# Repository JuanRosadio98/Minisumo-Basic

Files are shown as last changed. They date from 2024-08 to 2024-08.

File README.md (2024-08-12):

# Minisumo Nivel Senior
Robot Minisumo basado en ESP32, driver TB6612FNG, sensores JS40F y Qtr1A para principiantes en robotica de competencia

DIAGRAMA DE BLOQUES DE COMPONENTES DEL ROBOT



VISTS 3D DE ROBOT ENSAMBLADO



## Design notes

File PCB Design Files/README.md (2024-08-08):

- Esquematico

  Ruta: ESP32_RobotController_Modular\Project Outputs\Documentation
- Bottom Layer para imprimir

  Ruta: ESP32_RobotController_Modular\Project Outputs\Documentation
- Lista de materiales (BOM)

  Ruta: ESP32_RobotController_Modular\Project Outputs\Assembly
- Archivos de fabricacion (Gerbers)

  Ruta: ESP32_RobotController_Modular\Project Outputs\Fabrication





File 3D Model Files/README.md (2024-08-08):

Materiales recomendados: ABS, PETG, PLA

Materiales adiconales para el ensamble:
. 6 Tornillos M3 x 10mm
  Referencia: 
  
  https://es.aliexpress.com/item/1005005483354397.html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

- 4 Prisioneros M3 x 4mm
  Referencia:
  
  https://es.aliexpress.com/item/1005006790023154.html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,scm-url:1007.40050.354490.0,pvid:8e516edc-514a-40b4-a4dc-20a4244071bc,tpp_buckets:668%232846%238109%231935&pdp_npi=4%40dis%21PEN%212.44%211.44%21%21%214.53%212.67%21%40210324e517231562863025298e5644%2112000038308083836%21rec%21PE%21%21ABX&utparam-url=scene%3ApcDetailTopMoreOtherSeller%7Cquery_from%3A

Piezas impresas en 3D ensambladas:



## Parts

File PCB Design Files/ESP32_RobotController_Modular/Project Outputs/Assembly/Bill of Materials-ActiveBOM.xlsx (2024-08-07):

Name | Description | Designator | Quantity
220uF, 50V | WCAP-ATG8 Aluminum Electrolytic Capacitor, Radial, THT, D10xH12.5, 220uF, 50V | C1 | 1
47uF, 50V | WCAP-ATG8 Aluminum Electrolytic Capacitor, Radial, THT, D6.3xH11, 47uF, 50V | C2 | 1
Diode Schottky | Diodo Schottky SS36 3A 60 V | D1 | 1
Header 3P | WR-PHD Socket Header, THT, Vertical, pitch 2.54mm, 1 Row, 3P | J1, J2, J3, J4, J5, J6, J7 | 7
Bornera de 2 pines | WR-TBL Serie 111 Horizontal Entry Modular, Pressure Clamp, THT, pitch 5mm, 2p | J8, J9, J10 | 3
Header 4p | WR-PHD Socket Header, THT, pitch 2.54mm, Single Row, Vertical, 4p | J12 | 1
Resistor 0805 | SMD 0805 10Kohms | R1, R2, R3, R4, R5, R6, R7, R15, R16, R17 | 10
Resistor 0805 | SMD 0805 20Kohms | R8, R9, R10, R11, R12, R13, R14 | 7
XUNPU TS-1002S-07026C | 6mm 7mm Round Button 50mA Brick nogging 6mm SPST 12V SMD,6x6mm Tactile Switches ROHS | SW1, SW2, SW3 | 3
7805 SMD TO-252 | IC REG LINEAR 5V 1A DPAK | U1 | 1
TB6612FNG - Module | Driver Puente H TB6612FNG 1.2A | U2 | 1
ESP32 DevkitV1 | ESP32 DEVKIT V1 Wireless WiFi Bluetooth Placa de desarrollo Micro USB Dual Core | U3 | 1

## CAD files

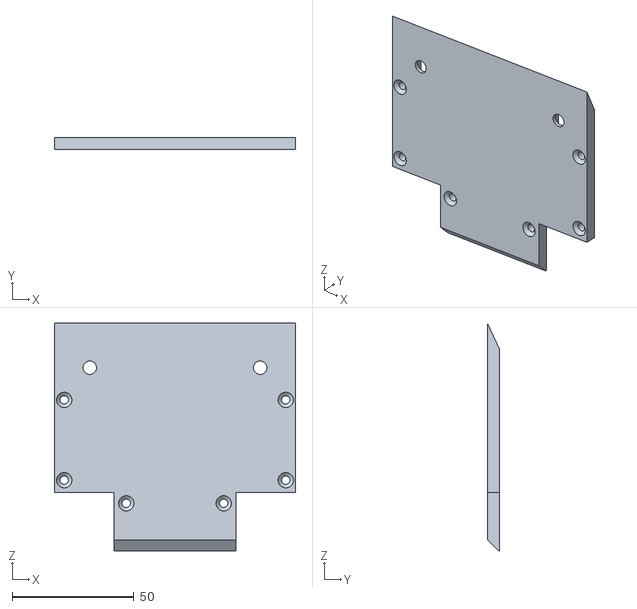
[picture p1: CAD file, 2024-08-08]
3D Model Files/STL/BaseTotal.stl
99.0 x 5.00 x 93.5

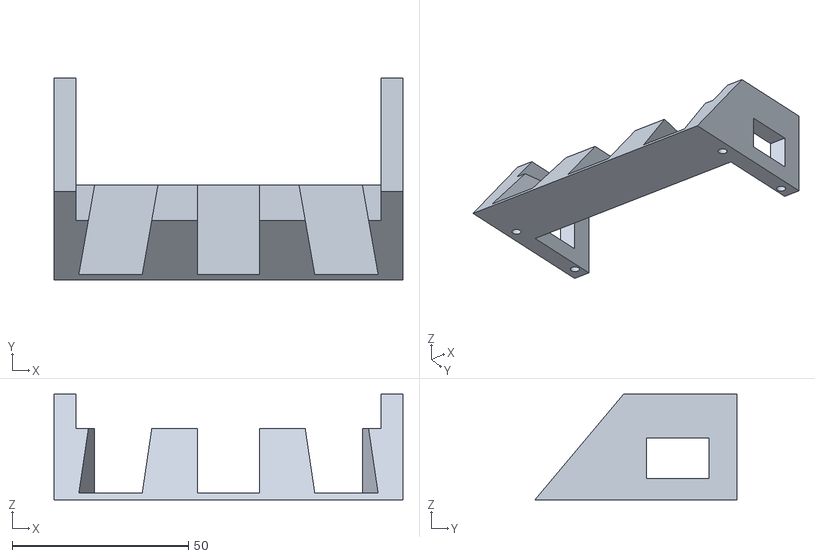
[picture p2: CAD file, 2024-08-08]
3D Model Files/STL/Cuerpo.stl
99.0 x 57.4 x 30.0

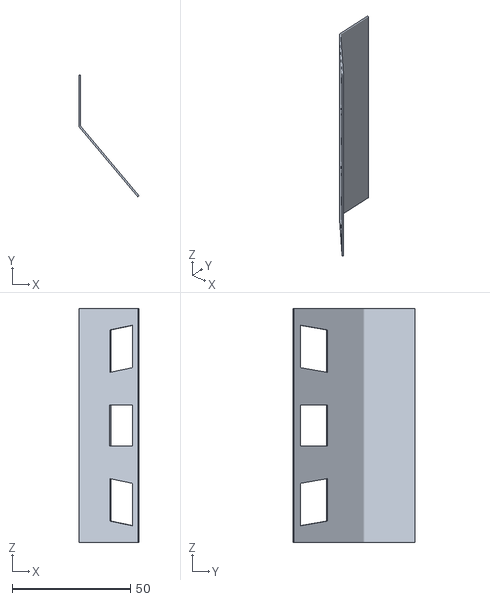
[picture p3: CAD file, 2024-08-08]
3D Model Files/STL/Cara.stl
25.4 x 51.5 x 99.0

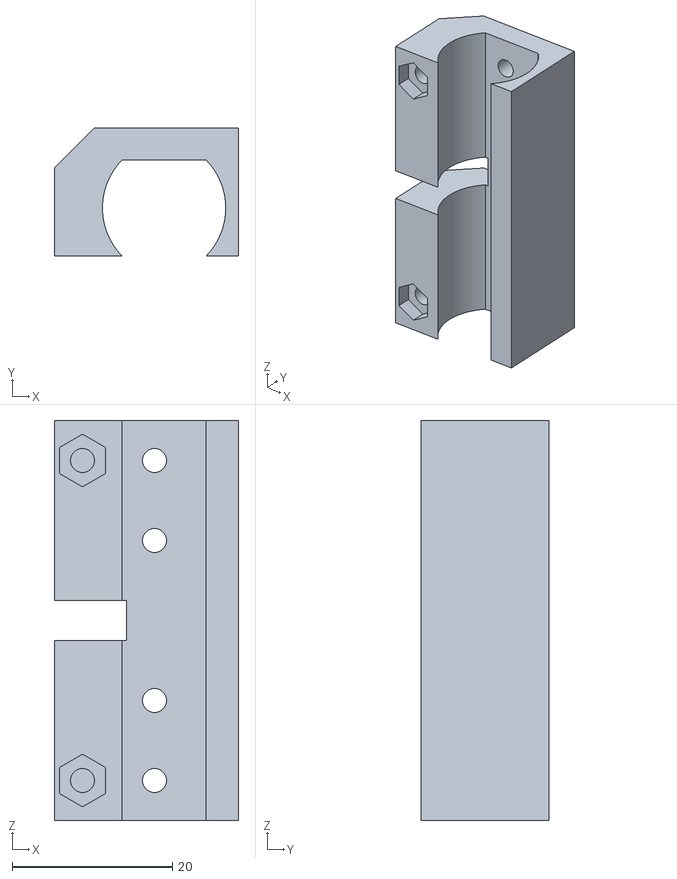
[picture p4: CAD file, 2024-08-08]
3D Model Files/STL/CajadeMotores Novamax H.stl
23.0 x 16.0 x 50.0

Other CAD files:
3D Model Files/BaseTotal.ipt
3D Model Files/CajadeMotores Novamax H.ipt
3D Model Files/Cara.ipt
3D Model Files/Cuerpo.ipt
3D Model Files/Ensamble.iam
3D Model Files/OldVersions/Ensamble.0001.iam

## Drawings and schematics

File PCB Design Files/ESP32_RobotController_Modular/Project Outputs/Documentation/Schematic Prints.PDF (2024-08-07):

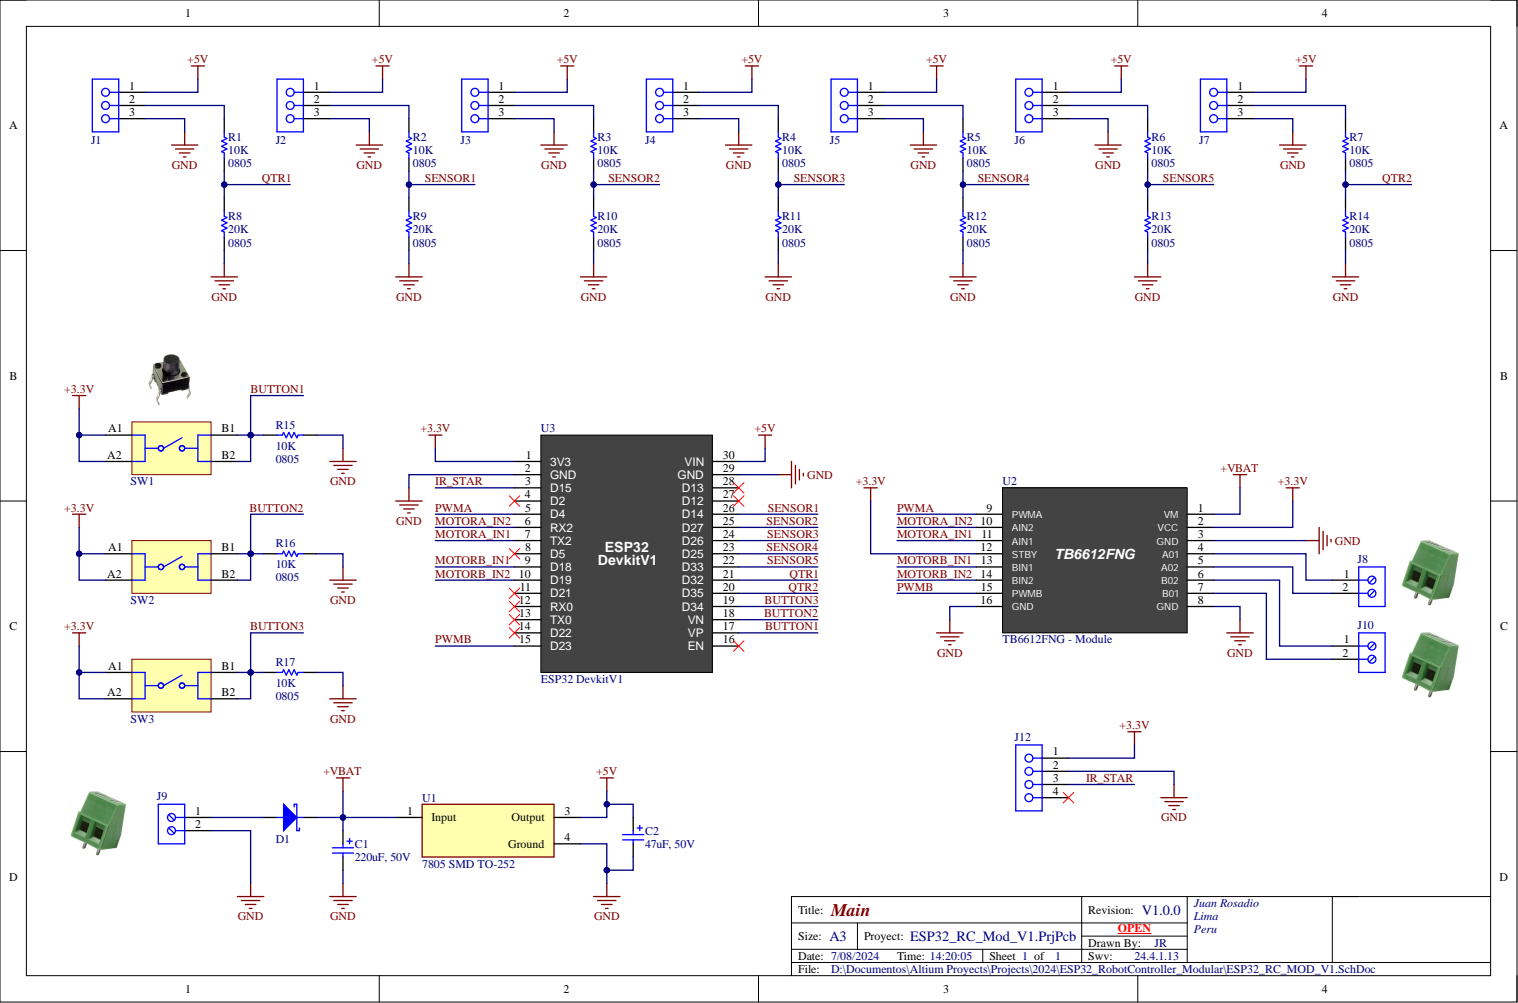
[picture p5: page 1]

D:\Documentos\Altium Proyects\Projects\2024\ESP32_RobotController_Modular\ESP32_RC_MOD_V1.SchDoc

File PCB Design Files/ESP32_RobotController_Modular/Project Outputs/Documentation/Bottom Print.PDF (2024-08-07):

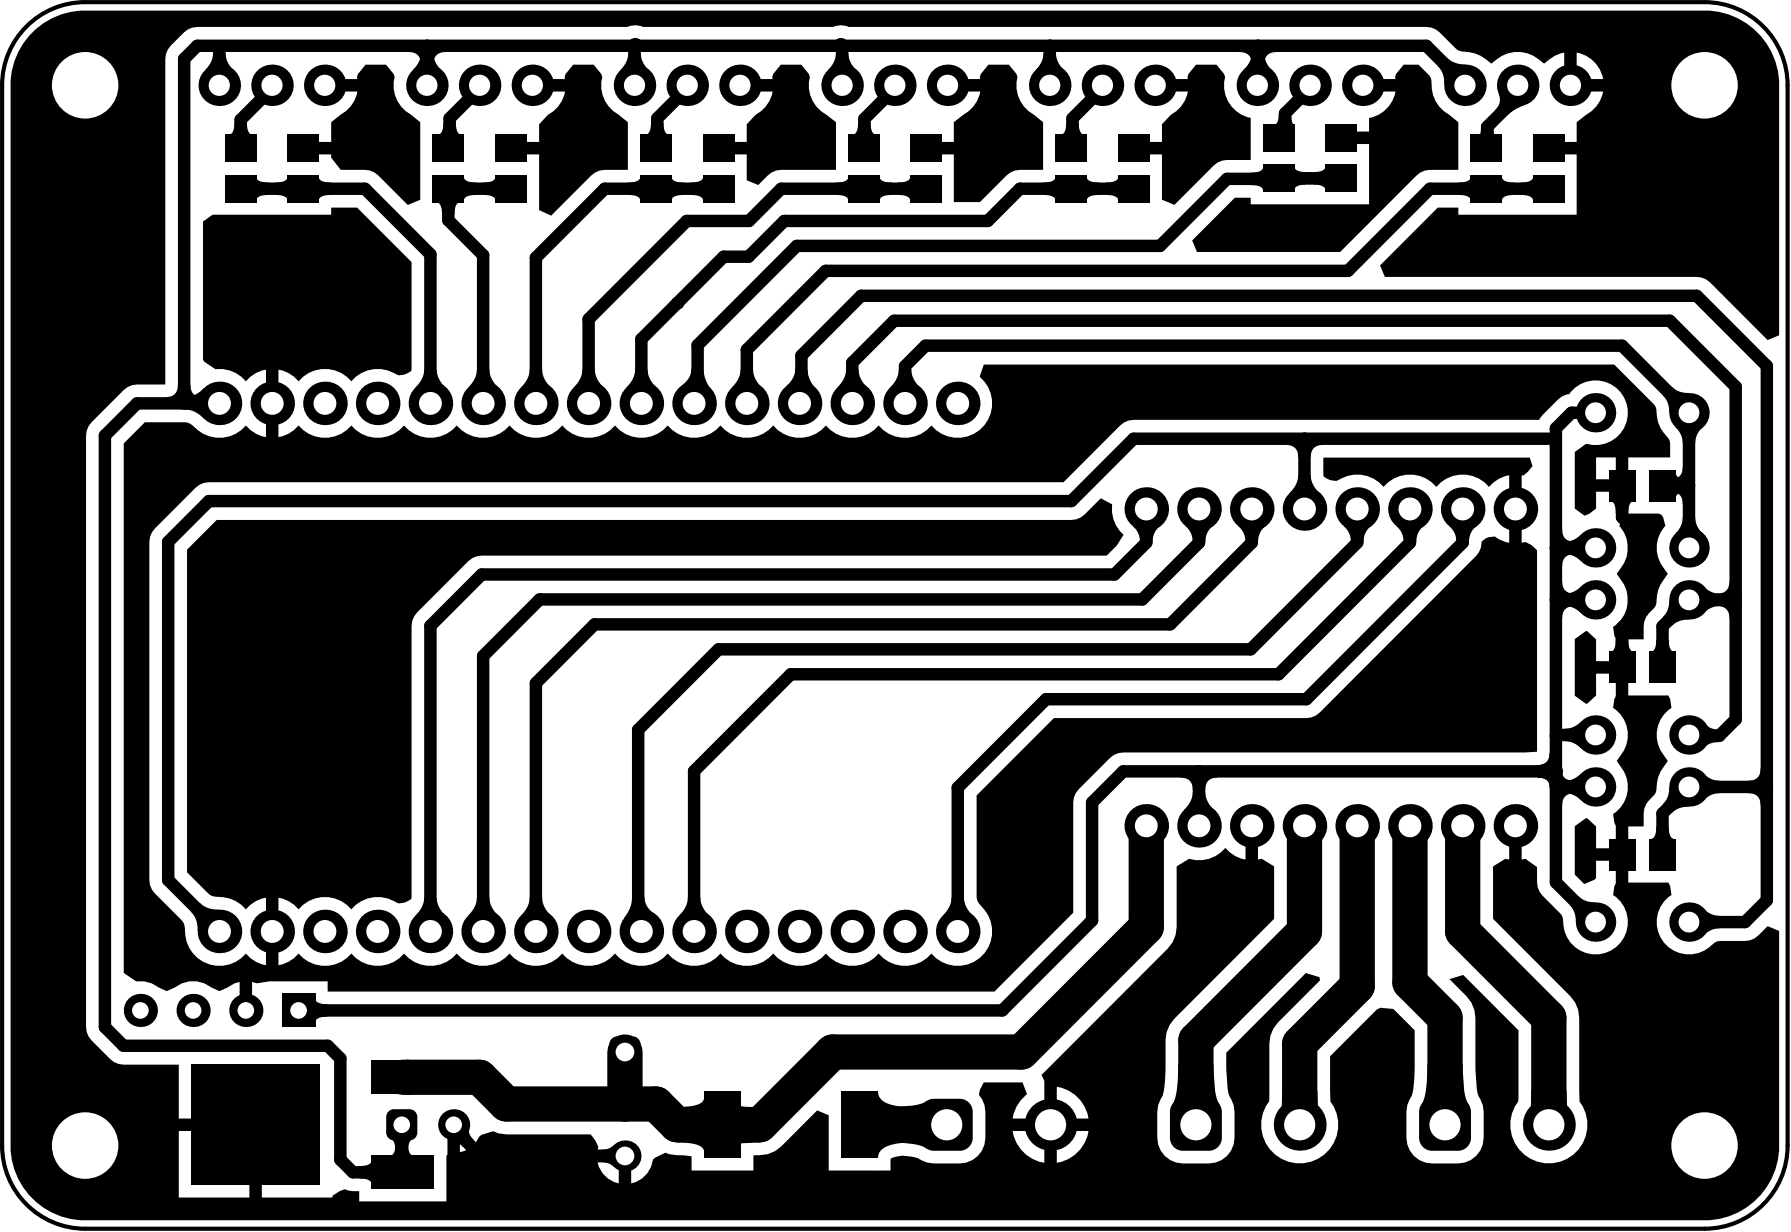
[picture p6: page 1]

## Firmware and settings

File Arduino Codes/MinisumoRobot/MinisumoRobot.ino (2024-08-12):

#define PUSH_1 36
#define PUSH_2 39
#define PUSH_3 34
//LINE SENSORS
#define QTR_1 32
#define QTR_2 35
//PRESENCE SENSORS
#define SENSOR_1 14
#define SENSOR_2 27
#define SENSOR_3 26
#define SENSOR_4 25
#define SENSOR_5 33

//REMOTE CONTROL
#define IR_STAR 15

#define USER_LED 2

//MOTOR DRIVER
#define MOTOR_PWMA 4
#define MOTOR_INA1 17
#define MOTOR_INA2 16

#define MOTOR_PWMB 23
#define MOTOR_INB1 18
#define MOTOR_INB2 19

#define TmCh_PWMA 0
#define TmCh_PWMB 1

int s_ii, s_i, s_c, s_d, s_dd, qtr_i, qtr_d, ctrl_star;
int strategy = 0;

void Push_Init(void);
void Motors_Init(void);
void Sensors_Init(void);

void setup() {
  // put your setup code here, to run once:
  Serial.begin(115200);
  Push_Init();
  Motors_Init();
  Sensors_Init();
  digitalWrite(USER_LED, LOW);

  Serial.println("Seleccione Estrategia(1-3): ");
  while (1) {
    if (digitalRead(PUSH_1) == 1) {
      digitalWrite(USER_LED, HIGH);
      while (1) {
        if (digitalRead(PUSH_1) == 0) {
          strategy++;
          digitalWrite(USER_LED, LOW);
          Serial.println(strategy);
          break;
        }
      }
    }

    if (digitalRead(PUSH_2) == 1 && strategy > 0) {
      digitalWrite(USER_LED, HIGH);
      while (1) {
        if (digitalRead(PUSH_2) == 0) {
          strategy--;
          digitalWrite(USER_LED, LOW);
          Serial.println(strategy);
          break;
        }
      }
    }

    if (digitalRead(PUSH_3) == 1) {
      while (1) {
        if (digitalRead(PUSH_3) == 0) {
          for (int i = 0; i < strategy; i++) {
            digitalWrite(USER_LED, HIGH);
            delay(500);
            digitalWrite(USER_LED, LOW);
            delay(400);
          }
          break;
        }
      }
      break;
    }
  }
  Serial.print("Strategy selected: ");
  Serial.println(strategy);

  while (ctrl_star == 0) {
    digitalWrite(USER_LED, HIGH);
    delay(100);
    digitalWrite(USER_LED, LOW);
    delay(100);
    Sensors_Read();
  }
}

void loop() {
  // put your main code here, to run repeatedly:
  switch (strategy) {
    case 1:
      Strategy_1();
      break;

    case 2:
      Strategy_2();
      break;

    case 3:
      Strategy_3();
      break;

    default:
      break;
  }
}

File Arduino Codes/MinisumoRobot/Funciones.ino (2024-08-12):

void Sensors_Read(void) {
  s_ii = digitalRead(SENSOR_1);
  s_i = digitalRead(SENSOR_2);
  s_c = digitalRead(SENSOR_3);
  s_d = digitalRead(SENSOR_4);
  s_dd = digitalRead(SENSOR_5);

  qtr_i = digitalRead(QTR_1);
  qtr_d = digitalRead(QTR_2);

  ctrl_star = digitalRead(IR_STAR);
}

void Sensors_Init(void) {
  pinMode(SENSOR_1, INPUT);
  pinMode(SENSOR_2, INPUT);
  pinMode(SENSOR_3, INPUT);
  pinMode(SENSOR_4, INPUT);
  pinMode(SENSOR_5, INPUT);

  pinMode(QTR_1, INPUT);
  pinMode(QTR_2, INPUT);

  pinMode(IR_STAR, INPUT);
}

void Push_Init(void){
  pinMode(PUSH_1, INPUT);
  pinMode(PUSH_2, INPUT);
  pinMode(PUSH_3, INPUT);
}

void Motors_Init(void)
{
  //Canal del Timer, Freq, Resolution
  ledcSetup(TmCh_PWMA, 10000, 10);
  ledcSetup(TmCh_PWMB, 10000, 10);
  //Pin, Canal del Timer
  ledcAttachPin(MOTOR_PWMA, TmCh_PWMA);
  ledcAttachPin(MOTOR_PWMB, TmCh_PWMB);

  pinMode(MOTOR_INA1, OUTPUT);
  pinMode(MOTOR_INA2, OUTPUT);
  pinMode(MOTOR_INB1, OUTPUT);
  pinMode(MOTOR_INB2, OUTPUT);

  digitalWrite(MOTOR_INA1, LOW);
  digitalWrite(MOTOR_INA2, LOW);
  digitalWrite(MOTOR_INB1, LOW);
  digitalWrite(MOTOR_INB2, LOW);

}

void Motors_Control(int pwmA, int pwmB)
{
  if (pwmA >= 0)
  {
    ledcWrite(TmCh_PWMA, pwmA);
    digitalWrite(MOTOR_INA1, LOW);
    digitalWrite(MOTOR_INA2, HIGH);
  }
  else
  {
    pwmA = pwmA * -1;
    ledcWrite(TmCh_PWMA, pwmA);
    digitalWrite(MOTOR_INA1, HIGH);
    digitalWrite(MOTOR_INA2, LOW);
  }

  if (pwmB >= 0)
  {
    ledcWrite(TmCh_PWMB, pwmB);
    digitalWrite(MOTOR_INB1, LOW);
    digitalWrite(MOTOR_INB2, HIGH);
  }
  else
  {
    pwmB = pwmB * -1;
    ledcWrite(TmCh_PWMB, pwmB);
    digitalWrite(MOTOR_INB1, HIGH);
    digitalWrite(MOTOR_INB2, LOW);
  }
}
